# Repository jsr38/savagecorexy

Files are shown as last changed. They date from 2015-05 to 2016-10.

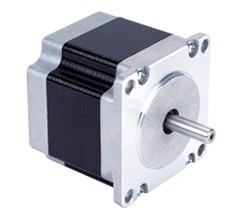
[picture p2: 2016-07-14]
datasheets/NEMA23-JKM-76mm_files/20131115143613461.jpg

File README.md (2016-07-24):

Savage CoreXY
=============

_NOTE_ This is still a work in progess, it is currently printing quite well.

This work was originally derived from [wolfmanjm/wolfhbot](https://github.com/wolfmanjm/wolfhbot) although since then it has diverged significantly and probably has very little in common now, although I retain the fork as provenance. 

A large build volume 3D printer based on the CoreXY concept.

It uses 4040 generic extrusions for most of the frame.

* The X carriage runs on Makerslide from [Amber Spyglass Ltd](http://amberspyglass.co.uk/)
* The Y carriages run on Makerslide from [Amber Spyglass Ltd](http://amberspyglass.co.uk/)
* The drive uses GT2 pulleys and belts
* the Belts have no cross over, they are stacked on top of each other instead
* build volume is large 300x1200x300 mm
* The Z platform has three stepper plus ballscrew Z actuators running on two 2040 Makerslides 
  with cast aluminium carriage. It runs on 1204 ballscrews.

Pictures and Videos
-------------------

* [first movements](https://youtu.be/KUbpFoaNcHg)
* [second movement](http://youtu.be/xxxxx)

Electronics and Firmware
------------------------

I used an Alligator Board with some modifications.  Details of the board are here:  [jsr38/AlligatorBoard](https://github.com/jsr38/AlligatorBoard)

My expansion board to allow alternative stepper drivers can be found here:  [jsr38/crocolulo](https://github.com/jsr38/crocolulo)

I'm currently running Repetier firmware on the Alligator.  My fork containing the current configuration is here: [jsr38/Alligator-Repetier-Firmware](https://github.com/jsr38/Alligator-Repetier-Firmware)

GT2 Belt Drive
--------------
The two end idlers are 2x flanged bearings back to back, and another pair separated with a washer above it,
Then two of the idlers on the X Gantry are raised to keep the belt riding level.
I avoid the cross over of the belts by running the two belts one above the other in parallel.

Z Bed
-----

The new Z actuator is a length of 500mm of 2040 VSlot, with a printed
carriage and v wheels. Driven by a McMaster ACME 1/2" leadscrew with
10TPI, Bearing blocks using 608 at top and bottom and a Nema17 with
5mm/0.25" flexible coupling. The bottom bearing block isolates the
flexible coupling from taking any weight and compressing. As the 1/2"
leadscrew is pretty big it has no wobble as far as I can tell and
having bearings top and bottom seems to be very stable. I also used a
printed Leadscrew nut printed in PLA and it seems pretty snug and
smooth. I also used a half height leadscrew nut and spring to implement
antibacklash which appears to be necessary.

There is a length of 2040 that spans from the Z actuator to the other
side of the frame where another 500mm length of 2040 VSlot has a vslot
mini carriage which is bolted to the end of the 2040 beam. Halfway
along this beam is a short piece of 2020 perpendicular to it, this
provides the third attachment point for the bed.

The most important part of this design is the
[moving knot](http://cockrum.net/cnc_mechanical.html), which is attached to
the top and bottom and runs over 4 v groove bearings on the cross
beam, This keeps the beam level while allowing a single actuator on one
end to move it up and down. This is the [far end](http://flic.kr/p/i67Sim),
and here is a view of the [whole assembly](http://flic.kr/p/i67Es7).

The bed is attached to the cross beam at three places to provide three
point bed levelling.  I use a scheme where a 4mm stud is screwed into
the tslots, and a 25mm length of aluminum rod, tapped to 4mm is
screwed onto that, this can be turned to move up and down the stud. At
the top of the aluminum is a cut out that the glass bed fits. Next to
this, and also bolted into the tslot, is an M4 bolt with a conical
spring bolted to the top, this pushes the glass at the three
attachment points up into the slots on the aluminum rounds. This keeps
the glass flat without deforming it, and allows it to be leveled at
three points by turning the aluminum rounds. Some jam nuts are used
to screw up to the aluminum rounds to stop them unscrewing once
levelled.

So this adds several printed parts... The Carriage, a bracket to hold
the leadscrew nut, and bearing blocks. Also some lathe work to cut a
thread into the center of some 1/2" aluminum round, and lathe a groove
at the top that the glass can slot into. (If the bed is not heated
this could be a printed part).

BOM
---
Aluminum parts are from Misumi with Misumi part numbers

* 10x 500mm HFS2020 20mm extrusions - frame
* 16x HBLFSN5 corner brackets - frame
* 2x  550mm HFS2020 - X Gantry sides
* 2x  85mm HFS2020 - X Gantry sides (Note it's cheaper to buy 2x 1000mm of 2020 and cut these yourself)
* 2x  540mm Makerslide - Y Rails
* 4x  HBLFSNF5 brackets - X Gantry
* 1x  500mm HFS2040 - Z Bed
* 1x  250mm HFS2020 - Z Bed
* 2x  Shapeoko motor mounts https://www.inventables.com/technologies/upgraded-shapeoko-motor-mount - Y carriages
* 12x VWheels https://www.inventables.com/technologies/dual-bearing-v-wheel-kit or http://openbuildspartstore.com/delrin-v-wheel-kit/
* lots of M5 nuts and bolts
* lots of M3 nuts and bolts
* 2x Nema 17 Stepper motors (preferably Kysan or equivalent)

Belt Drive
----------
* 10 meters GT2 belt
* 2 x GT2 pulleys 20 tooth
* 12 x 5mm flanged bearings for the idlers 

Printed Parts
-------------
* 1x motor-bracket-l.stl
* 1x motor-bracket-r.stl
* 1x x-carriage.stl

Z bed
-----
* 1x Nema 17
* 1x lead screw (McMaster 1/2" 10TPI ACME)
* Two printed Leadscrew nuts and a collar for the anti backlash
* 5/8" diameter spring for the anti backlash
* 2x 500mm 2040 VSlot
* 4x solid V Wheels http://openbuildspartstore.com/solid-v-wheel-kit/
* 1x printed Z carriage, plus leadnut holder
* 1x mini vslot carriage and mini wheels http://openbuildspartstore.com/mini-v-wheel-plate/
* 4x v groove bearings, 2x turnbuckles, two lengths of Spectra fishing line for the moving knot

Construction
------------

Getting the top of the frame square is essential, measure each end of the Y
rails to make sure they are parallel. Next the belts need to have exactly the
same tension to keep the X gantry straight, this was introducing non-square
prints for me. Loosen the X gantry on both Y carriages so it sits loosely on
the Y carriages, then measure the distance of each end of the X Gantry to the
front corner of the frame. Now tighten one or other belt until the X Gantry is
square to the Y rails, then tighten it down to the Y carriages.

If you find cylinders print out oblong or squares are not square this is
probably the problem.

License
-------

CC BY SA

<br /><span xmlns:dct="http://purl.org/dc/terms/" property="dct:title">WolfHBot</span> by <a xmlns:cc="http://creativecommons.org/ns#" href="http://wolfmanjm.github.com/wolfhbot" property="cc:attributionName" rel="cc:attributionURL">Jim Morris</a> is licensed under a <a rel="license" href="http://creativecommons.org/licenses/by-sa/3.0/deed.en_US">Creative Commons Attribution-ShareAlike 3.0 Unported License</a>.<br />Based on a work at <a xmlns:dct="http://purl.org/dc/terms/" href="https://github.com/wolfmanjm/wolfhbot" rel="dct:source">https://github.com/wolfmanjm/wolfhbot</a>.

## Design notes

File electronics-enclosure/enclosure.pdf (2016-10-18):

Made with Laser Cutter Ruby Gem (v1.0.3) Credits to Prawn for ruby PDF generation, and BoxMaker for inspiration.

Online: http://makeabox.io/
Source: https://github.com/kigster/laser-cutter units:
width:
height:
depth:
thickness:
notch:
kerf:
stroke:
padding:
margin:
page_size:

mm
250.0
250.0
50.0
3.0
30.0
0.06096
0.0254
2.54
3.175
custom

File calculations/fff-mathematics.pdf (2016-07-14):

# The Mathematics of Fused Filament Fabrication

### J. S. Reeve Independent Researcher

jsr [at] jsreeve.org

### July 14, 2016

## 1 Drive Mechanisms

### 1.1 Core XY

Equations of motion for a Core XY system are:

### 1.2 Delta

### 1.3 Drive Belts

For an endless belt, what is the circumference required to fit two pullies, radii r1, r2 and separation, d?

l = π (r1 + r2) + 2q
s

2 + (r2 − r1)

2
(1)

!!! This assumes r1 ≈ r2 !!! TODO

### 1.4 Steps per Unit Distance

Steps per millimeter of travel in the X direction:

1

## 2 Polymer Extrusion

### 2.1 Extruder Calibration

### 2.2 Volumetric Extrusion

## 3 Temperature

### 3.1 Thermistor Calibration

Thermistors, both NTC and PTC, and thermocouples are all used to sense temperatures at various critical locations on and around a typical FFF machine. See the Wikipedia page relating to thermistors: https://en.wikipedia.org/wiki/Thermistor. (https://en.wikipedia.org/wiki/Thermistor) A widely used third-order model developed for semiconductor resistance is the Steinhart-Hart equation.

1
T

= a + b ln(R) + c(ln(R))³ k(ln(R))² (2)

Coefficients a, b and c can be determined from empirically acquired data using a fitting method, in this case we choose least squares approximation. Starting from acquired data 1:
Summarising the least squares process and relating it to the numpy/scipy implementation referenced here: https://github.com/jsr38/savagecorexy/blob/cuboid/scripts/thermistor_calibration.py. (https://github.com/jsr38/savagecorexy/blob/cuboid/scripts/thermistor_calibration.py)
The general idea is to minimise the following norm:

kb − Axk

2

Suppose we took n measurements where:

x =

a
b
c
- , b =

1
T1

1
Tn

A =

1 | 1 | 1 | . . . | 1
ln(R1) | ln(R2) | ln(R3) . . . ln(Rn)
ln(R1)

3
| ln(R2)

3
| | ln(R3)

3
. . . ln(Rn)

3

This can be achieved by inversion of the matrix A. The following concerns the detail of generating a suitable lookup table given a circuit configuration and ADC of known resolution, that achieves the best resolution over our region of interest.

2

Resistance R | Temperature T
(k ohms) | (degrees celsius)
18.0 | 70.0
18.4 | 68.0
20.0 | 66.5
23.5 | 60.0
28.7 | 55.5
38.1 | 48.8
68.0 | 34.0
74.1 | 32.0
79.8 | 30.3
84.3 | 29.0
92.2 | 27.3
96.4 | 26.3
100.3 | 25.3
107.0 | 23.9
112.6 | 22.8
114.2 | 22.4
115.7 | 22.1
117.3 | 21.8
120.0 | 22.0
130.0 | 20.0

Table 1: Thermistor measurements peformed in lab.

The function used to generate lookup tables within the Repetier firmware assumes a different model, the β model which discounts the third order effects:

| 1
| T =

1
| T0

+

1
β

ln
R
R0
(3)

We could derive β and supply a pair of points to this function in order to generate a lookup table but since we have the third-order approximation we may as well use this to generate the lookup table. The accompanying script assumes a pull-up or pull-down resistor which linearises the thermistor response and hence reduces error introduced by finite resolution ADC, quantisation error, over our region of interest.

| N = 2B , B = 12, ∆b = 2B−L = 2⁴ = 16

3

n =

0 2¹ 2

2
. . . 2

L

αn =

n∆b +

∆b − 1
2

+

1
2

α =

α0 | α1 | α2 | . . . αn
=

Vo
Vi
Results of running the process on our data:

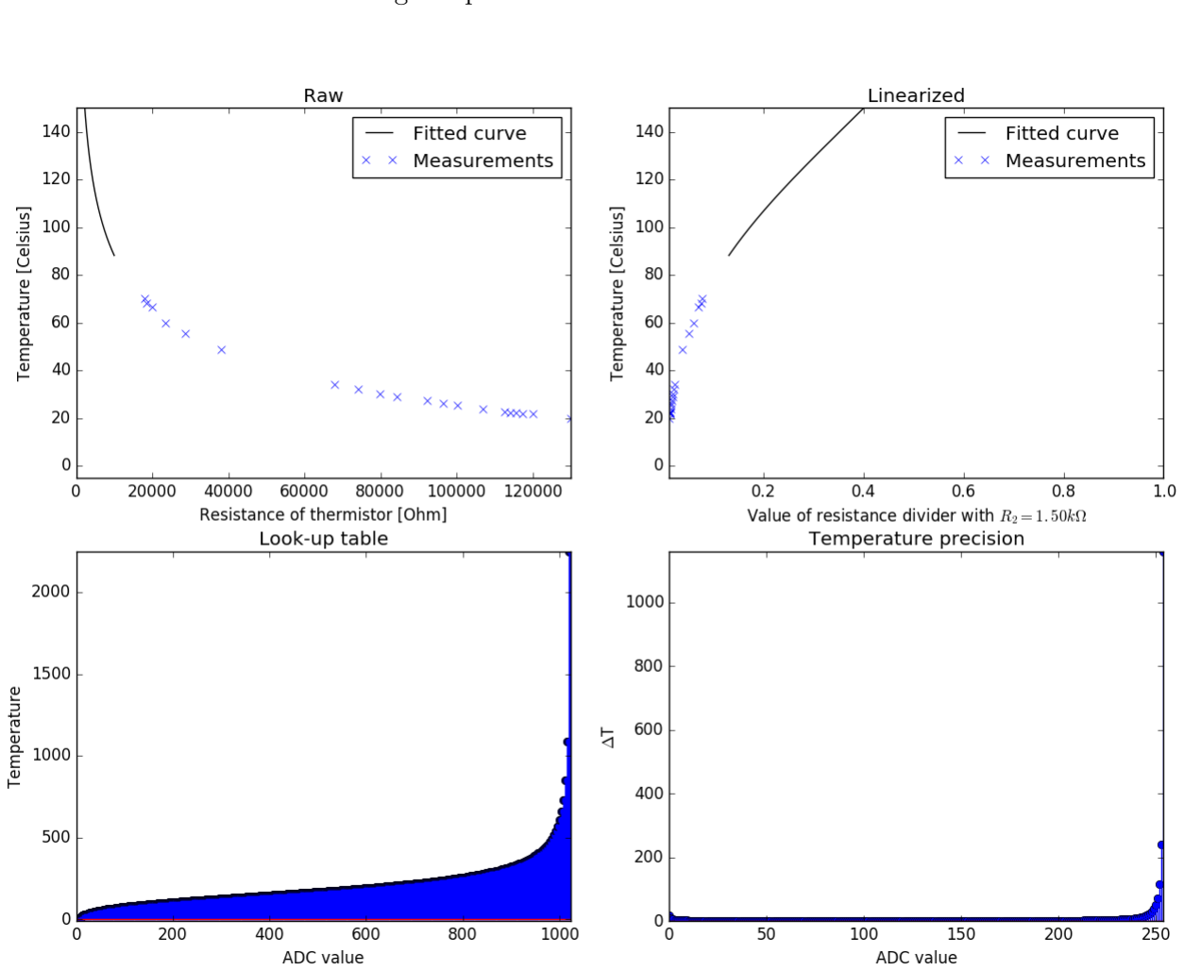
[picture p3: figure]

4

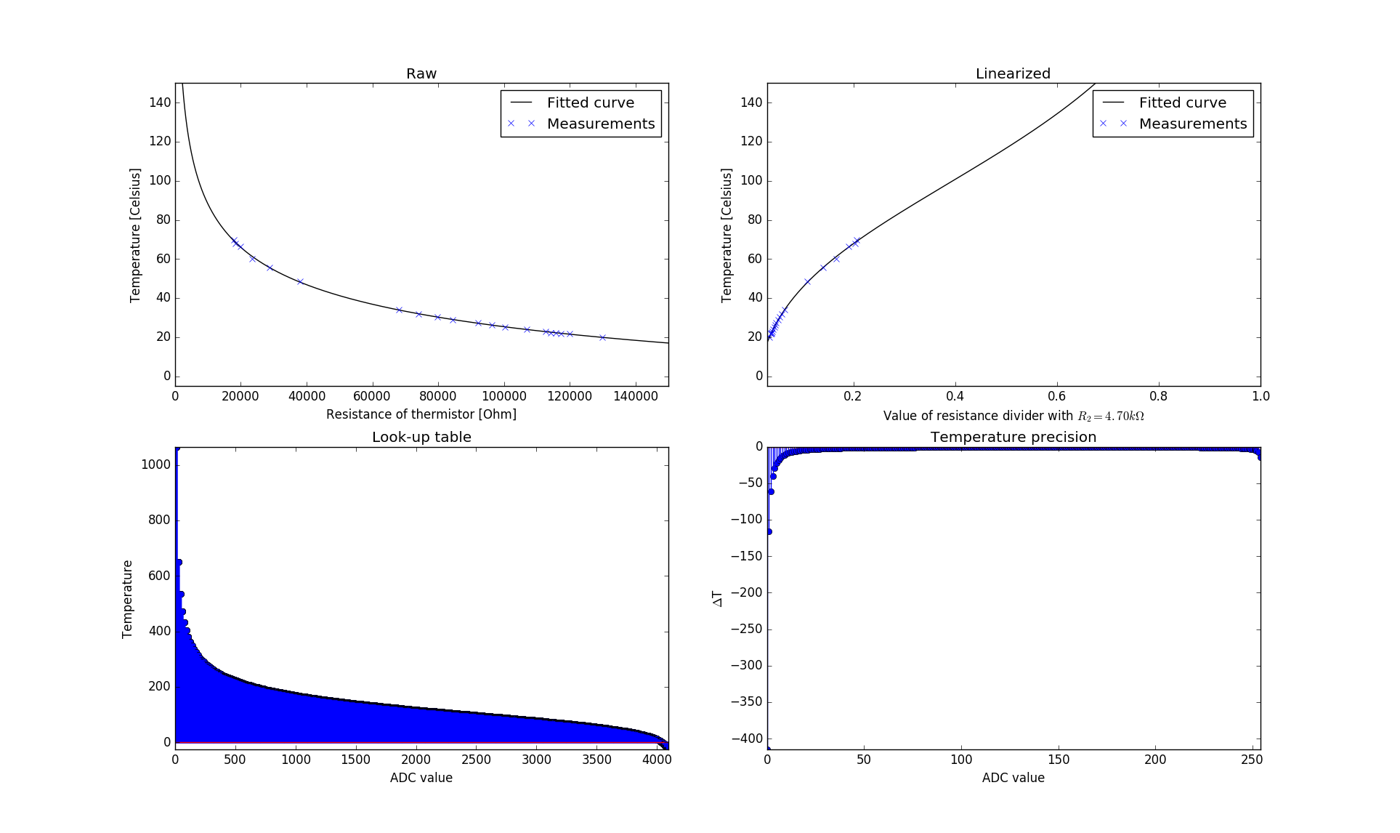
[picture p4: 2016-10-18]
scripts/thermistor_analysis.png

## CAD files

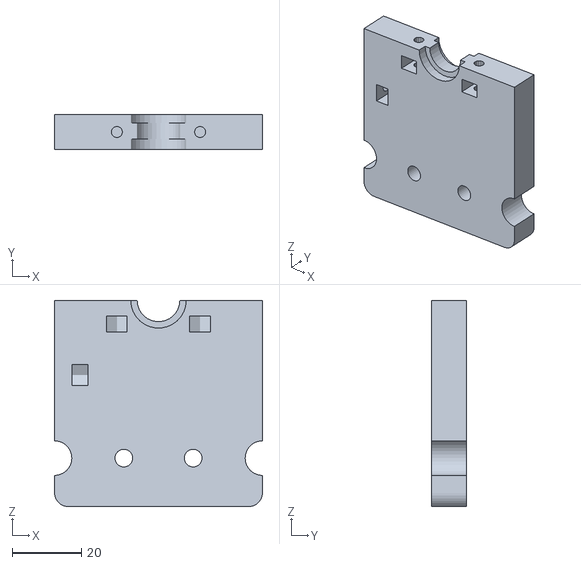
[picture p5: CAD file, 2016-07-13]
stl/E3D_clone_hot_end_mount_w_proximity_sensor_mountV2-main.stl
60.0 x 10.0 x 59.5

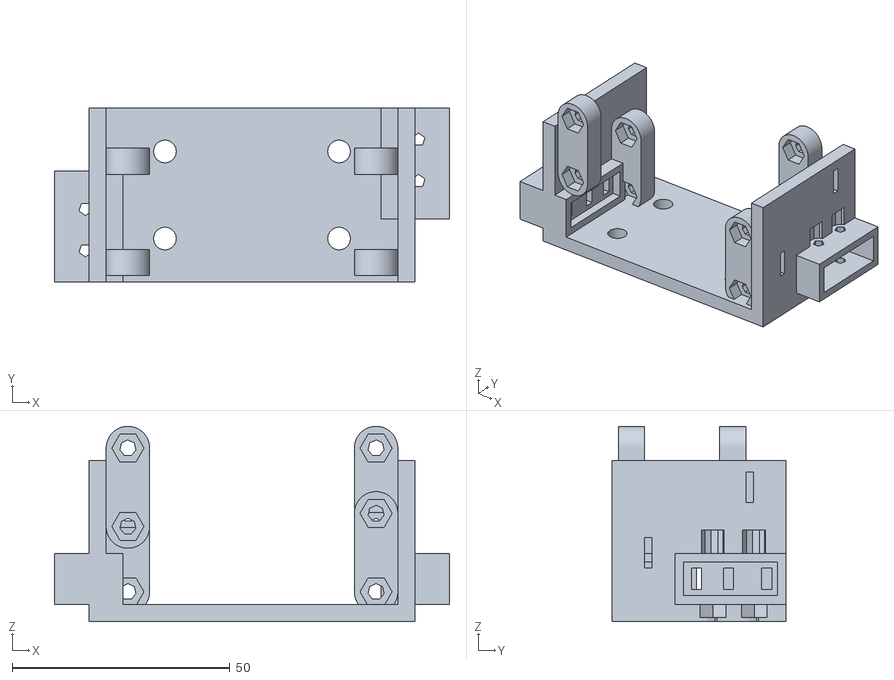
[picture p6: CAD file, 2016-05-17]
carriage-belt-clamp.stl
90.8 x 40.0 x 44.9

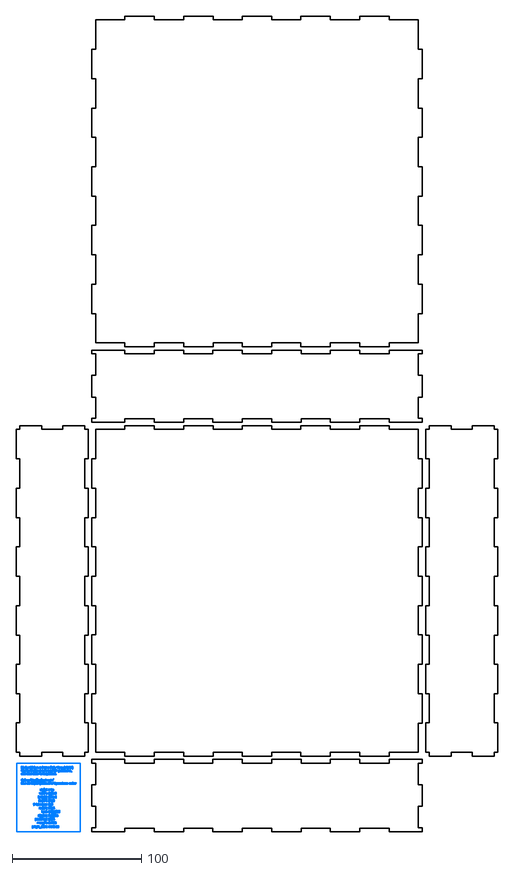
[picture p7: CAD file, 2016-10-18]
electronics-enclosure/enclosure.dxf
373.1 x 631.7

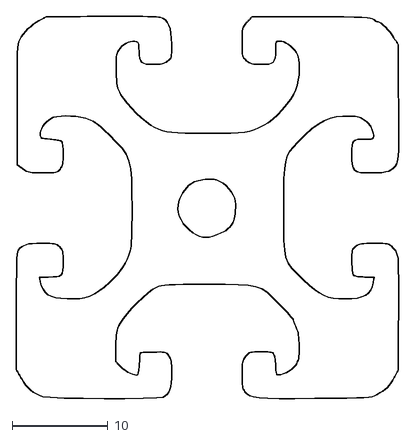
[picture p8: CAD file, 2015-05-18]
kjn/extrusion.dxf
40.0 x 40.0

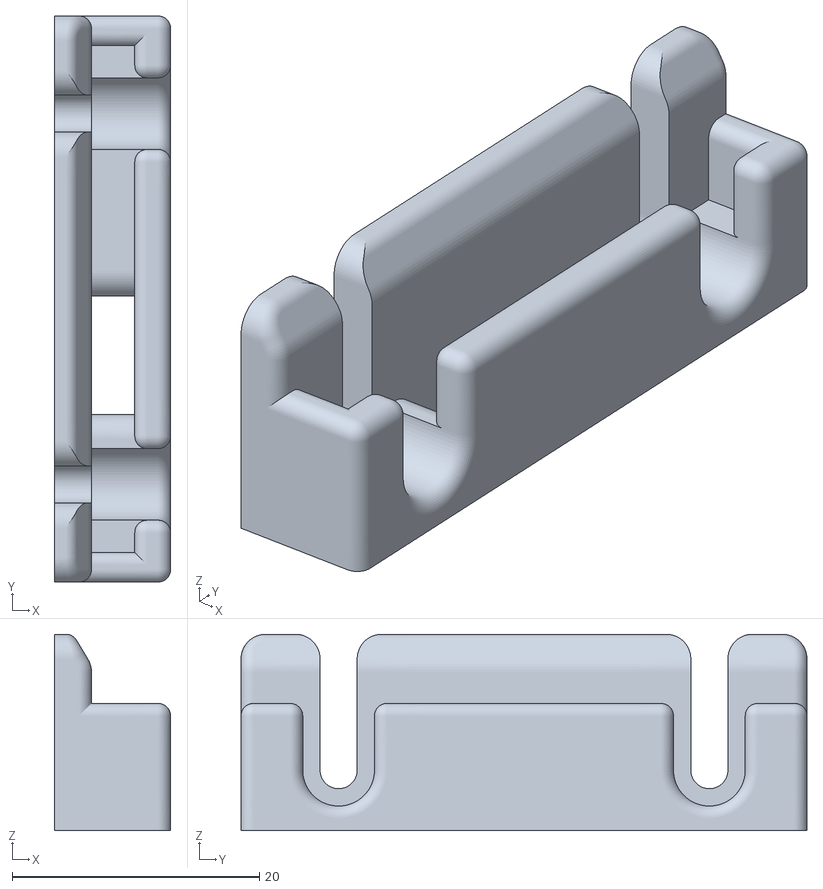
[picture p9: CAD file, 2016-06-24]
stl/fanduct/FanDuct-Bracket.stl
9.40 x 45.8 x 15.9

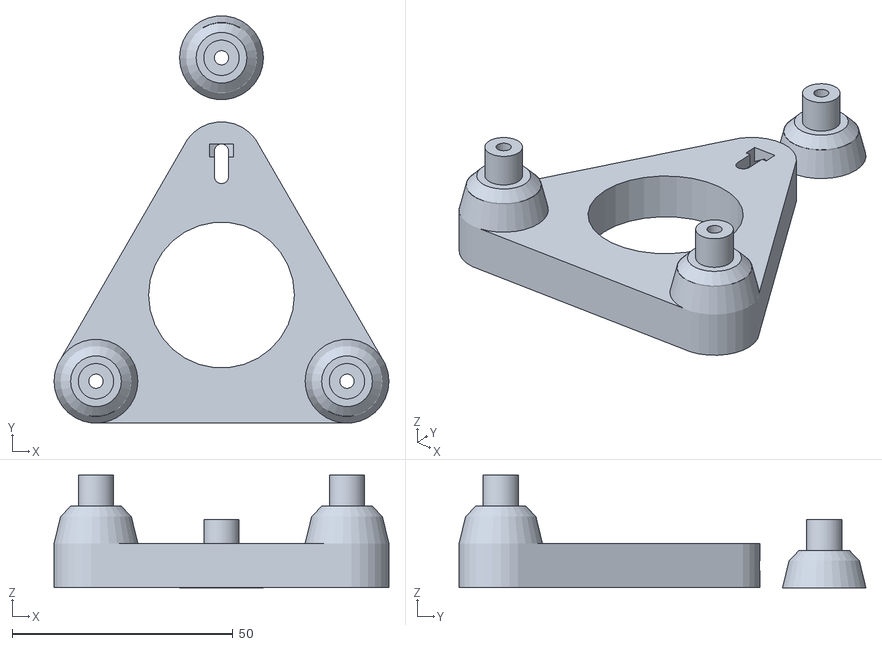
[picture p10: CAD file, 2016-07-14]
stl/y-carriage-src.stl
75.8 x 92.1 x 25.5

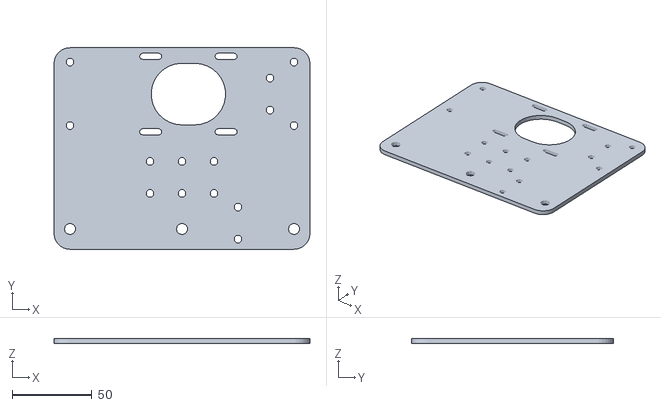
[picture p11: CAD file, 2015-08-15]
carriage_plate_motor_c14006_rev_1.stl
160.0 x 126.0 x 3.17

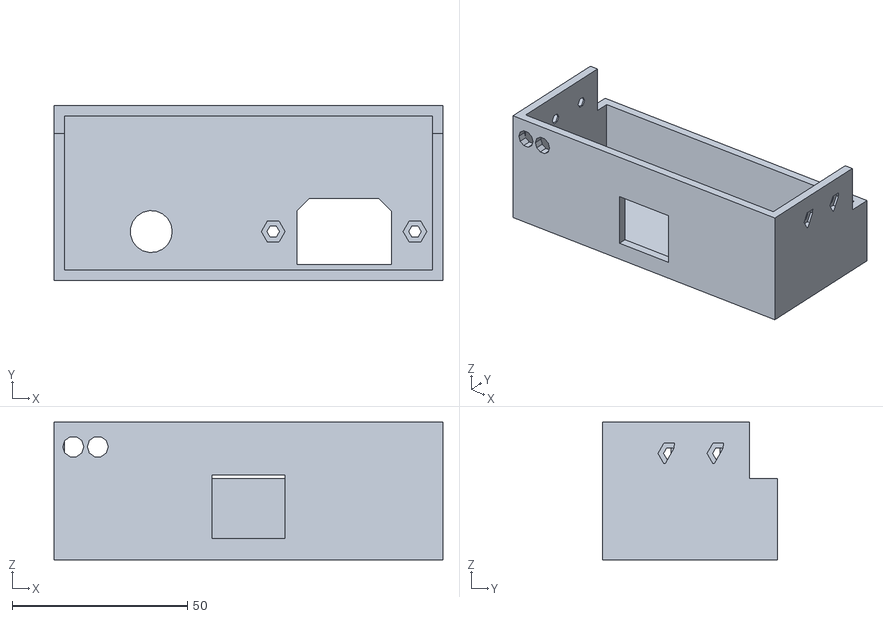
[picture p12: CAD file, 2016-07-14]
stl/power_supply_cover.stl
111.0 x 50.0 x 39.2

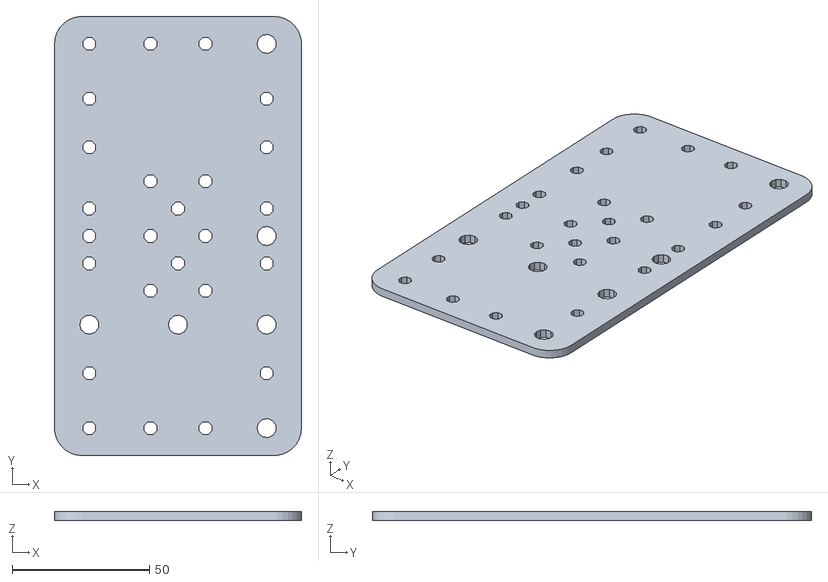
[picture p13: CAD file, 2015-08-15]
carriage_plate_standard_c14005_rev_2.stl
90.0 x 160.0 x 3.17

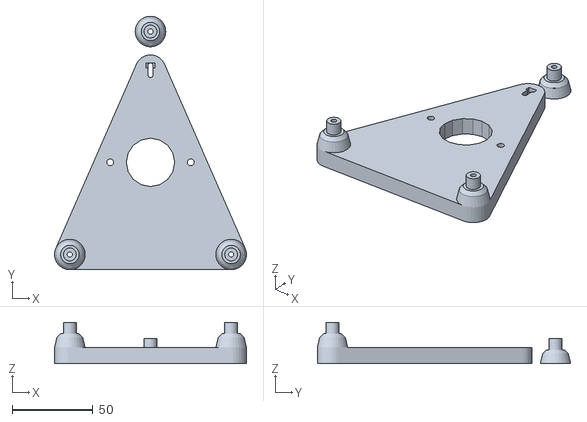
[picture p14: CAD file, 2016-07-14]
stl/x-carriage-src.stl
119.0 x 157.1 x 25.5

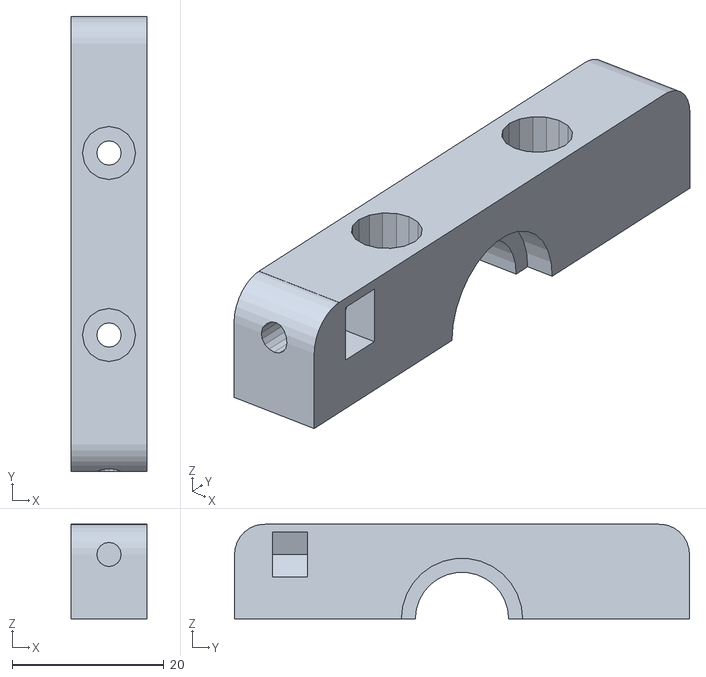
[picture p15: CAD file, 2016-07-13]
stl/E3D_clone_hot_end_mount_w_proximity_sensor_mountV2-clip.stl
10.0 x 60.0 x 12.5

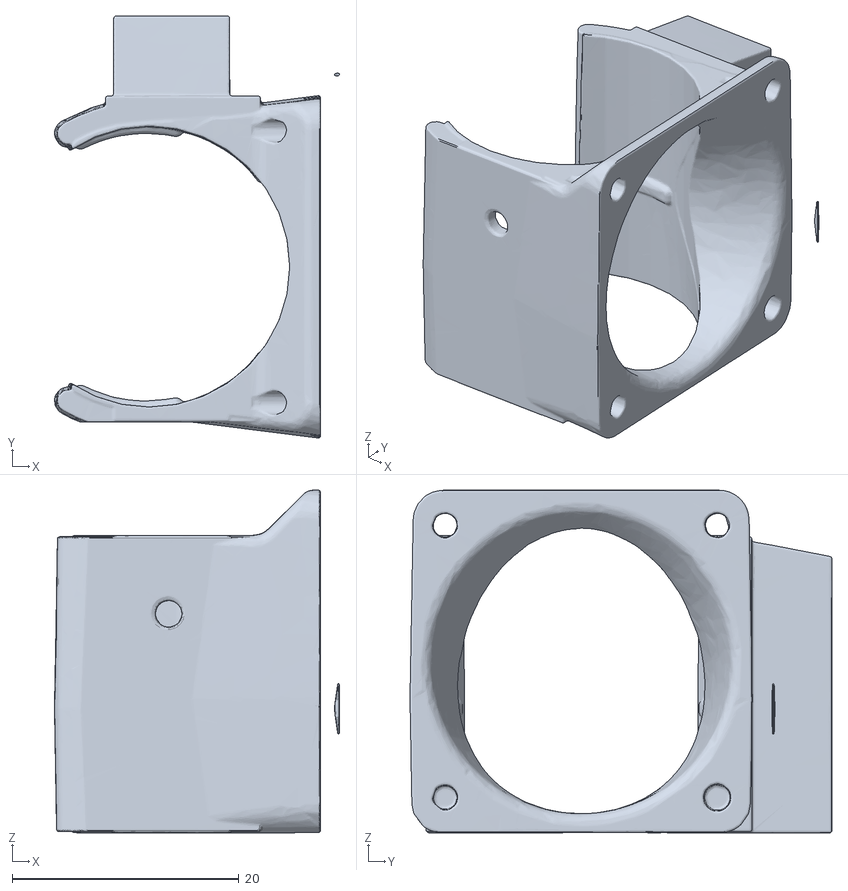
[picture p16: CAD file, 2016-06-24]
stl/E3DFANDUCT_.stl
25.2 x 37.2 x 30.2

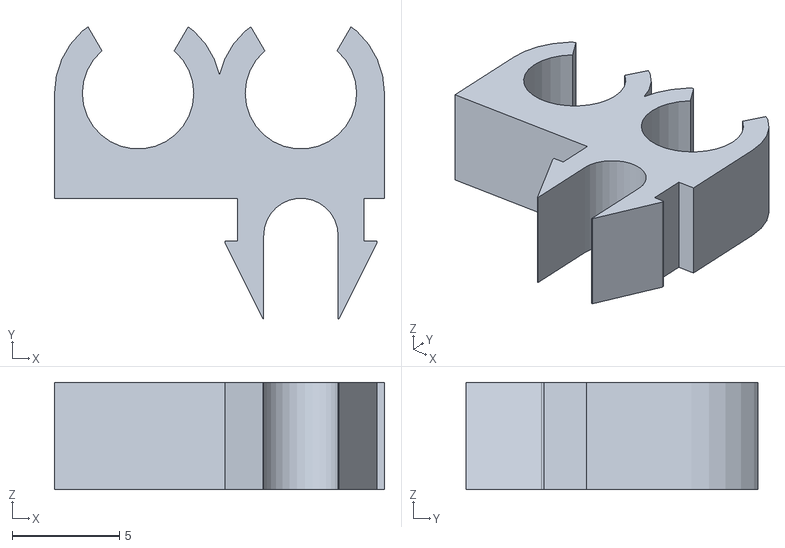
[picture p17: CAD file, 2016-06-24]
stl/Clip-060-double.stl
15.4 x 13.6 x 5.00

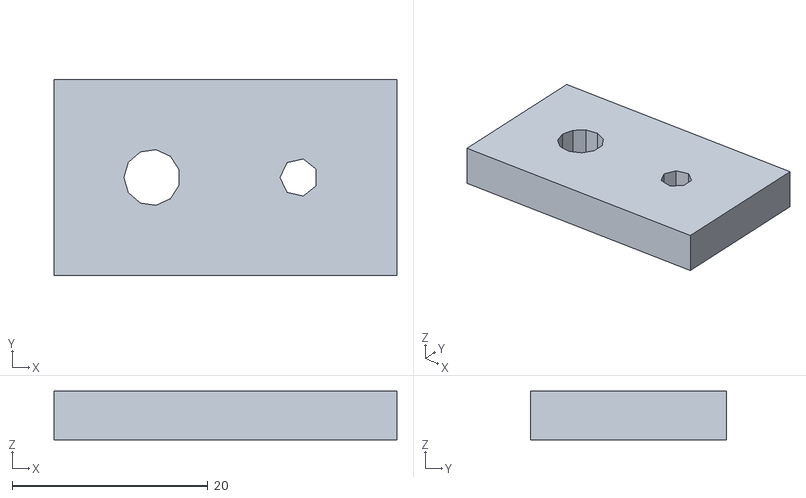
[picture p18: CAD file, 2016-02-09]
stl/electronics-mount-alligator.stl
35.0 x 20.0 x 5.00

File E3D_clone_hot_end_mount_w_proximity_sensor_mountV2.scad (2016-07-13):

//
//Mount for E3D hotend clone with mount for 18mm diameter proximity sensor
// this is designed to be bolted in place of the stock folgertech extruder,
// or any extruder mounted with holes the same width as Nema17 motor screws
//    this is part of the conversion to a bowden setup
// Designed by Lee Buell
// version1.0 December 30, 2015
// GPL v3.0
//  released under Creative Commons - Attribution - Share Alike licence (CC BY-SA)
//////////////////////////////////////////////////////////////////////////////////////
// it uses two libraries from the mendel90 design, available from here:
//
// https://github.com/T3P3/Mendel90/tree/LaserCut/scad
// teardrops.scad
// utils.scad
//
//
// this was designed for the E3D clone hot ends, by changing the JHeadDiameters below, it might work with a genuine E3D hot end
//  Explanation of JHeadDiameters numbers:
//    the first is the width of the narrow part of the mount (top)
//    the second is the  width of the wide part of the mount (top)
//    the third is the width of the bottom cooling fin area, I don't have a genuine E3D, but I believe this third number is the one to change



JHeadDiameters = [12.3, 16, 25];
JHeadDimensions = [4.05, 4.05+4.8, 12.3, 18.3, 50.1];

FanMountingHoleWidth=32; //32 for a 40mm fan
FlangeThickness=8;  // Thickness of mounting flange and Hot end mounting plate
HotendHeight=25;  // height of Hot End mount on mounting flange
FanWidth=40;
FanMountPitch = 30.0; // Mounting hole pitch for ducted fan
FlangeExtension=32.0;   //Length beyond fan with for hot end to mount
FlangeLength=FanWidth+FlangeExtension;// - 5.0;  //Total flange length
HotEndHeatSinkWidth=25; //width of heat sink, ?? for E3D  25 for chinese E3D clone
HotEndMountingThinArea=12.5;  //Thin band on the top of the HE
HotEndMountingWideArea=16.5;  //Wide bands on the top of the HE
HotEndMountingThinAreaHeight=5;  //Height of thin band
HotEndMountingWideAreaHeight=13;  //Height of wide band
ProxSensorDiameter=18.5;  //Diameter of proximity sensor
ProxSensorNutDiam=28.5;   //Diameter of proximity sensor nuts
ProxSensorLockWasherDiam=31;   //Diameter of proximity sensor LockWashers
ProxSensorDiameterMountFlangeWidth=ProxSensorNutDiam+7.5;
DistanceBetweenHE_Sensor=2;  //distand between the hot end and the proximity sensor
MountingHoleDistance=sqrt((FanMountingHoleWidth/2*FanMountingHoleWidth/2)*2);
CornerRadius=4;

CarriageMountHolePitch = 20;


print_clearance=0.1; //additional clearance between two printed objects

$fn=30;

rotate([-90,0,0])
translate([25,-FlangeThickness/2,30])
difference(){
CompleteHotEndMount();
translate([0,-(ProxSensorDiameterMountFlangeWidth+DistanceBetweenHE_Sensor+HotEndHeatSinkWidth/2+5)-50,0])
cube([100,100,100], center=true);
}
!difference(){
rotate([-90,0,90])
translate([25,(ProxSensorDiameterMountFlangeWidth+DistanceBetweenHE_Sensor+HotEndHeatSinkWidth/2+5),35])
CompleteHotEndMount();
translate([0,30,-50])
cube([120,100,100], center=true);
}


module CompleteHotEndMount(){
 difference(){
    union(){
      //Flange that mounts to x-carriage
      //mounting_flange();
	  
	   //Flange to mount Hot end
      translate([0,-FlangeExtension,-HotendHeight])
      rounded_rectangle([FanWidth + 20,FlangeLength,FlangeThickness+2],CornerRadius);

      }  //union
	  
      // Cavities
      // hole for proximity sensor
      //translate([0,-20,-40])
      //ProxSensorHole();
      
      
	  // hole for jhead mount
	  echo(ProxSensorDiameterMountFlangeWidth+DistanceBetweenHE_Sensor+HotEndHeatSinkWidth/2+5);
      translate([0,-(ProxSensorDiameterMountFlangeWidth+DistanceBetweenHE_Sensor+HotEndHeatSinkWidth/2+5),-HotendHeight-6])	  
      rotate([180,0,0])
      JHead(JHeadDiameters, JHeadDimensions);
	  
      // Mount holes for carriage
      translate([( - CarriageMountHolePitch) / 2.0,-10.0,-HotendHeight]) cylinder(r= 2.55, h = FlangeThickness + 4.0, center = true);
      translate([( CarriageMountHolePitch) / 2.0,-10.0,-HotendHeight]) cylinder(r= 2.55, h = FlangeThickness + 4.0, center = true);
      
	  
      // Cutout for V-wheel nuts on carriage
      translate([( - CarriageMountHolePitch * 3) / 2,-10.0,-HotendHeight]) cylinder(r= 5, h = FlangeThickness + 4.0, center = true);
      translate([( CarriageMountHolePitch * 3) / 2,-10.0,-HotendHeight]) cylinder(r= 5, h = FlangeThickness + 4.0, center = true);
      
      // holes for retainer cap	 
	  translate([12,-(FlangeLength+1),-25])
	  rotate([90,0,180])
	 Locknut_and_screwhole(Screwlength=16,DepthOfNut=22);
	 translate([-12,-(FlangeLength+1),-25])
	  rotate([90,0,180])
	  Locknut_and_screwhole(Screwlength=16,DepthOfNut=22);
	  
      // Holes for fan mount
      translate([-47,-FlangeLength + 8.0,-25]) rotate([90,0,90]) Locknut_and_screwhole(Screwlength=16,DepthOfNut=22);
      translate([-47,-FlangeLength + 8.0 + FanMountPitch,-25]) rotate([90,0,90]) Locknut_and_screwhole(Screwlength=16,DepthOfNut=22);
      
  } //difference
}  //module

module Locknut_and_screwhole(Screwlength=16,DepthOfNut=15){
//hole for m3 bolt followed by hex hole for m3 locknut
//hole for m3 bolt - with tight fit

nutheight=4.6;  // height of locknut as it sits flat on a table  // 4.5 when printed so nut is oriented flat, 4.5 was tight due to a stray hanging part of filament
LocknutDiamater=6.9;  //  Diameter of locknut with extra clearance added so it drops in but still grips the nut without slipping  //7.1 slipped - too large
screwheaddiamater=7;  //diamter of the head of the screw
ScrewheadHoleDiam=screwheaddiamater+.3; // remember the added value on the end witll be cut in half since since openscad uses radius measurements

LengthBeforeNut=DepthOfNut;
LengthAfterNut=3;

TotalNutLength=DepthOfNut+nutheight+LengthAfterNut;
RecessedHeadDepth=(TotalNutLength-1.5)-Screwlength;

//recessed hole for m3 screw
translate([0,0,-1])
cylinder(h=RecessedHeadDepth+1,r1=screwheaddiamater/2,r2=screwheaddiamater/2, center = false, $fn=16);

//hole for m3 screw
translate([0,0,0])
cylinder(h=TotalNutLength,r1=3/2+.1,r2=3/2+.1, center = false, $fn=16);

// hole for m3 locknut
translate([0,0,DepthOfNut])
rotate([0,0,30])    //rotate the flat sides of the hex nut
cylinder(h=nutheight,r1=LocknutDiamater/2,r2=LocknutDiamater/2, center = false, $fn=6);

//hole to drop nut into
translate([-LocknutDiamater/2+.475,-15,DepthOfNut])
rotate([0,0,0])   cube([(sqrt(3)*(LocknutDiamater/2)),15,nutheight]);
}  //module

module JHead(diameters = [12, 16, 25], dimensions = [3.7, 9.3, 12.3, 18.3, 50.1]) {
    color("Red") {
      // Top of JHead
      translate([0,0,-dimensions[0]])
        cylinder(d=diameters[1], h=dimensions[0]);
      translate([0,0,-dimensions[1]-0.01])
       cylinder(d=diameters[0], h=dimensions[1]-dimensions[0]+0.5);
      translate([0,0,-dimensions[2]])
        cylinder(d=diameters[1], h=dimensions[2]-dimensions[1]+.3);
      translate([0,0,-dimensions[3]])
        cylinder(d=9, h=dimensions[3]-dimensions[2]);
      translate([0,0,-dimensions[4]]) {
        // Radiator Volume
        cylinder(d=diameters[2], h=dimensions[4]-dimensions[3]);
        translate([0,0,-10]) {
          // Throat
          cylinder(d=6, h=10);
          // Heating Block
          translate([0,5,0])
            cube([20,20,10], center=true);
          // Nozzle
          translate([0,0,-12])
            cylinder(d1=1, d2=5, h=3);
          translate([0,0,-9])
            cylinder(d=10, h=5, $fn=6);
        }
      }
    }
  }

module HotEndMountHole(){
      //thin par of Hot end neck
     cylinder(h=20, r=HotEndMountingThinArea/2, $fn=20);
     // top wide part of Hot end neck
     translate([0,0,-15])
     cylinder(h=20, r=HotEndMountingWideArea/2, $fn=20);
     // bottom wide part of Hot end neck
     translate([0,0,10])
     cylinder(h=10, r=HotEndMountingWideArea/2, $fn=20);

}  // module

module ProxSensorHole(){
  //round hole for sensor
  cylinder(h=80, r=ProxSensorDiameter/2, $fn=20);
  //hex hole for nut
  translate([0,0,-2]) rotate([0,0,30])
  cylinder(h=40, r=ProxSensorNutDiam/2, $fn=6);
}  // module
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

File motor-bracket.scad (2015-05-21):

use <misumi-parts-library.scad>;
use <MCAD/stepper.scad>
use <MCAD/motors.scad>
use <MCAD/triangles.scad>
use <motor-mount.scad>
use <myLibs.scad>

thick= 5.6;
w= 54;
h= 55;

%translate([-20,20,0]) corner();
motor_bracket(1);

module motor_bracket(r=0) {
	mirror([0,r,0]) difference() { 
		union() {
			rotate([0,0,90]) corner_bracket();
			translate([thick,50/2+10,0]) rotate([0,0,-90])  motorPlate(thick, thick);
		}
		// mounting holes
		#translate([-1,10,h+3]) rotate([0,90,0]) hole(5, thick+2);
		translate([-1,20+25,20]) rotate([0,90,0]) slot(d=5, l=30,ht=thick+2);
		translate([-10,-thick-1,h]) rotate([0,90,90]) hole(5, thick+2);
		translate([-10,-thick-1,h-h/3]) rotate([0,90,90]) hole(5, thick+2);
		translate([-10,-thick-1,h/4]) rotate([0,90,90]) hole(5, thick+2);	}

}

module motorAttachment(thickness=4) {
        translate([0,h,thickness]) rotate([180,0,0]) difference() {
                cube([w,h,thickness]);
                translate([w/2,h/2,-1]) linear_extrude(height=thickness+2) stepper_motor_mount(17,8,true,0.1);
        }
}

module attachmentPlate(thickness=4) {
	cube([w,40,thickness]);
}

module buttress(thickness=4) {
        triangle(50, 40, thickness);
}

module motorPlate(thickness=4, buttressThickness=4) {
        union() {
                motorAttachment(thickness);
                translate([0,0.1,0]) rotate([90,0,0]) attachmentPlate(thickness);
                translate([buttressThickness,-0.1,0]) rotate([0,-90,0]) buttress(buttressThickness);
                translate([w,-0.1,0]) rotate([0,-90,0]) buttress(buttressThickness);
        }
}


module corner() {
	translate([10,0,10]) hfs2020(80);
	translate([0,-10,10]) rotate([0,0,90]) hfs2020(80);
	translate([10,-10,0]) rotate([90,0,0]) hfs2020(80);
}

module corner_bracket() {
	translate([-thick,-thick,0]) union() {
		cube([20+thick,thick,h+20-thick]);
		cube([thick,20+thick,h+20-thick]);
		translate([20,0,0]) cube([40,thick,40]);
	}
}

//module smount(w=50,l=50) {
//	translate([0,0,thick/2]) difference() {
//		cube([w,l,thick], center=true); 
//		translate([0,0,-thick/2-1]) linear_extrude(height= thick+2) stepper_motor_mount(nema_standard=17,slide_distance=5, mochup=false, tolerance=0.1);
//	}
//}

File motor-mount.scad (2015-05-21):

use <MCAD/motors.scad>
use <myLibs.scad>
use <MCAD/triangles.scad>

w= 54;
h= 50;

function motorMountWidth() = w;
function motorMountHeight() = h;

module motorAttachment(thickness=4) {
	translate([0,h,thickness]) rotate([180,0,0]) difference() {
		cube([w,h,thickness]);
		translate([w/2,h/2,0]) linear_extrude(height=thickness+1) stepper_motor_mount(17,5,true,0.1);
	}
}

module attachmentPlate(thickness=4) {
	difference() {
		cube([w,40,thickness]);

		// attachment holes
		#translate([(w/2)-10, 10, 0]) rotate([0,0,90]) slot(d= 5, l=10, ht=thickness);
		#translate([(w/2)-10, 30, 0]) rotate([0,0,90]) slot(d= 5, l=10, ht=thickness);
		#translate([(w/2)+10, 10, 0]) rotate([0,0,90]) slot(d= 5, l=10, ht=thickness);
		#translate([(w/2)+10, 30, 0]) rotate([0,0,90]) slot(d= 5, l=10, ht=thickness);
	}
}

module buttress(thickness=4) {
	triangle(50, 40, thickness);
}

module motorPlate(thickness=4, buttressThickness=4) {
	translate([-w/2, thickness, 0]) union() {
		motorAttachment(thickness);
		translate([0,0.1,0]) rotate([90,0,0]) attachmentPlate(thickness);
		translate([buttressThickness,-0.1,0]) rotate([0,-90,0]) buttress(buttressThickness);
		translate([w,-0.1,0]) rotate([0,-90,0]) buttress(buttressThickness);
	}
}

motorPlate(5, 5);
//motorAttachment();
//attachmentPlate();
//buttress();

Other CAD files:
stl/PCB_ALLIGATOR.STL
stl/shim_10mm.stl
stl/nema23-z-mount.stl
stl/drill-guide-z.stl
Clip-060.scad
Pulley_T-MXL-XL-HTD-GT2_N-tooth.scad
ballscrew_lower.scad
ballscrew_upper.scad
ballscrew_z_mount.scad
ballscrew_z_mount_centre.scad
bedleveller.scad
belt-clamp_GT2.scad
bracket4040.scad
carriage-belt-clamp.scad
drill-guide-z.scad
drill-guide.scad
drill_guide_makerslide.scad
dxf/b17022_rev_2.dxf
electronics-enclosure/enclosure.scad
electronics-mount-alligator.scad
foot.scad
hbot-frame.scad
hex-nut.scad
idler-gantry-v2.scad
idler-plate.scad
idler-v2.scad
kjn-parts-library.scad
microswitch-cutout.scad
nema23-z-mount.scad
power_supply_cover.scad
rounded-box.scad
shim_10mm.scad
src/motor-mount.scad
src/sprocket_with_tolerance.scad
stl/ballscrew_lower.stl
stl/ballscrew_upper.stl
stl/ballscrew_z_mount.stl
stl/ballscrew_z_mount_centre.stl
stl/drill-guide.stl
stl/drill_guide_makerslide.stl
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

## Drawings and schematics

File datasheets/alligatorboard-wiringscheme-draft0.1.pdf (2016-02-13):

Alligator Board – Wiring Diagram | draft 0.1

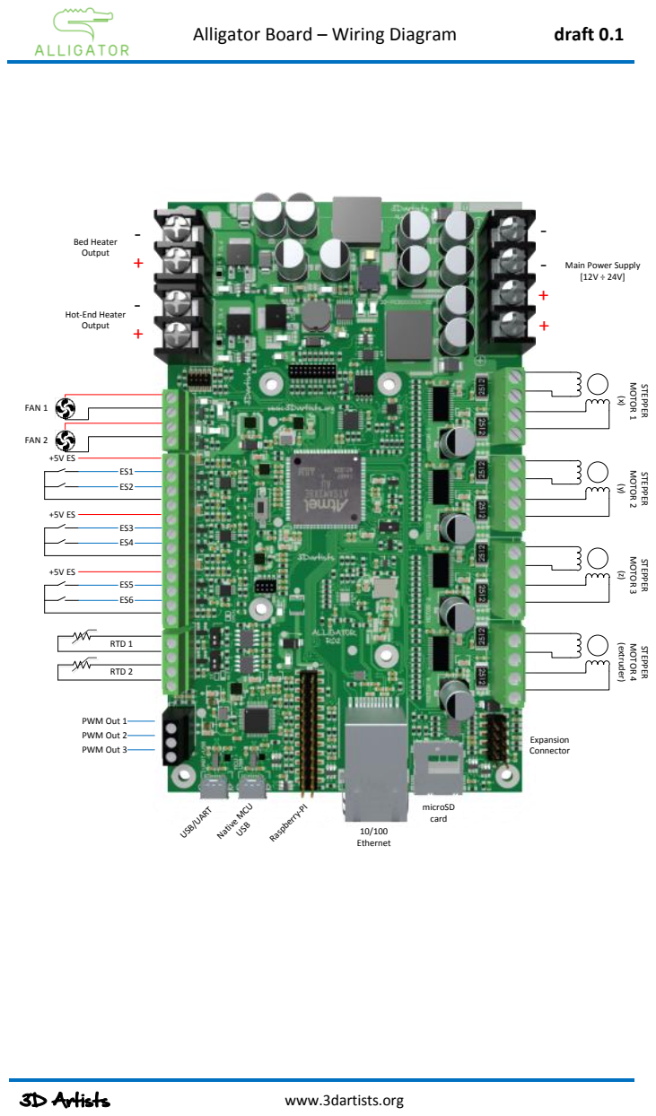
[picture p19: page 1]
3D Artists; www.3dartists.org; FAN 1; FAN 2; RTD 1; RTD 2; USB/UART; Raspberry-PI; 10/100 Ethernet; microSD card; Expansion Connector

STEPPER MOTOR 1 (x) STEPPER MOTOR 2 (y) STEPPER MOTOR 3 (z) STEPPER MOTOR 4 (extruder) Main Power Supply [12V ÷ 24V] -

Bed Heater Output

Hot-End Heater Output

PWM Out 1 PWM Out 2 PWM Out 3

Native MCU USB

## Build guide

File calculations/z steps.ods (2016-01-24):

mm/rotation | steps/rotation | microsteps | length | h | d | minh | maxd
2.54 | 3200 | 16 | 165 | 200 | 10 | 72.9451848993 | 148
layer ht | steps/mm | mm/step | tiers |  |  | min | max
0.3 | 1259.842519685 | 0.000793750 | 1 |  | max error between | 65 | 320 | mm | 216 | $H$216
 |  | 0.012700000 |  |  | 0.00444 |  |  |  | 1066 | $H$1066
 |  |  |  | max d | 299.48295 | travel |  |  |  |  |  | max error
 |  |  |  | min d | 0.00007 | 299.4828876009 |  |  |  |  |  | 0.00039375
 |  | 165
layer ht | h | d | Absolute steps | actual step | actual d | actual h | error in ht mm |  | steps | actual steps | actual move | error
0.3 | 0.15 | 164.9999318182 | 0.0858983714 | 0 | 165 | 0 | 0.15 |  | 377.9527559055 | 378 | 0.3000375 | 0.0000375
0.6 | 0.3 | 164.9997272725 | 0.3435936984 | 0 | 165 | 0 | 0.3 |  | 755.905511811 | 756 | 0.600075 | 0.000075 | 0.000075
0.9 | 0.45 | 164.9993863625 | 0.7730866201 | 1 | 164.99920625 | 0.5117976846 | 0.0617976846 |  | 1133.8582677165 | 1134 | 0.9001125 | 0.0001125 | 0.0001125
1.2 | 0.6 | 164.9989090873 | 1.3743782012 | 1 | 164.99920625 | 0.5117976846 | 0.0882023154 |  | 1511.8110236221 | 1512 | 1.20015 | 0.00015 | 0.00015
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

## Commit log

2015-05-19 Make frame a cuboid rather than a cube. WIP
    [hbot-frame.scad]
2015-05-21 correct path for MCAD imports and add 4040 bracket first pass
    [bedleveller.scad, bracket4040.scad, leadscrew-bearing-block.scad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]
2015-05-24 y-carriage extrusion width to 40mm
    [y-carriage.scad]
2015-05-24 Add a foot for the upright frame extrusions
    [foot.scad, rounded-box.scad]
2015-05-25 Improve foot by removing central pillar. Otherwise it'd be a tighter fit as we scale the extrusion up to give some extra tolerance.
    [foot.scad, foot.stl]
2015-05-25 Add metric-cerberus as submodule as we depend on mushroom() and extrusion4040_no_hole(), well, eventually we will.
2015-05-25 Use extrusion that scales each surface of the shape in the direction of the normal of the interface between plastic and air - more room
    [foot.scad, foot.stl]
2015-05-31 Add a drilling guide for drilling the aluminium profile extrusion.
    [drill-guide.scad, drill-guide.stl]
2015-06-03 Improve drill guide and fix a few bugs.
    [drill-guide.scad, drill-guide.stl, foot.scad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]
2015-06-04 Make the drill guide holes larger, now 2mm diameter. Add 1mm to the radius of the previously 4mm radius support structures for the guide holes.
    [drill-guide.scad, drill-guide.stl]
2015-06-12 Add pulley source and modify drill guide to correct scale factor bug and reduce dril holes to 1.75mm diameter
    [Pulley_T-MXL-XL-HTD-GT2_N-tooth.scad, drill-guide.scad, drill-guide.stl]
2015-06-13 Add a motor mount for NEMA23 stepper motor.
    [nema23-mount.scad, nema23-mount.stl]
2015-07-31 Update xy motor mount to have mounting holes along the horizontal extrusion rather than the vertical where the Makerslide rails are screwed in
    [nema23-mount.scad]
2015-08-15 Add idler-gantry-v2 and add switch to generate either left or right xy motor mount
    [carriage_plate_motor_c14006_rev_1.stl, carriage_plate_standard_c14005_rev_2.stl, idler-gantry-v2.scad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]
2015-08-15 Countersink mount screws
    [idler-gantry-v2.scad]
2015-08-15 Correct height for gantry idler
    [idler-gantry-v2.scad]
2015-08-16 Create idler model (non-carriage version). Refactor idler into idler top and bottom plate. Modify motor mounts to sit at correct height with gap to allow belt to pass through. Add Jospeh Prusa's GT2 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
    [belt-clamp_GT2.scad, carriage-belt-clamp.scad, idler-gantry-v2.scad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]
2015-08-22 +5mm offset for motor boss
    [nema23-mount.scad]
2015-10-25 Add drill guides to drill the z axis frame parts.
    [drill-guide-z.scad, drill-guide-z.stl, drill_guide_makerslide.scad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]
2015-11-17 Add ballscrew upper support
    [ballscrew_upper.scad]
2015-12-13 Modify ballscrew_upper to suit Makerslide
    [b17022_rev_2.dxf, ballscrew_lower.scad, idler-gantry-v2.scad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]
2015-12-27 Develop ballscrew_z_mount and add pdf of Makerslide profile
    [ballscrew_z_mount.scad]
2016-01-02 Tweak tolerances. Ahem... Include them where they should have been.
    [ballscrew_z_mount.scad]
2016-01-03 Add centre z ballscrew mount. TODO: cut the extrusion profile a bit longer instead of this nonsense :)
    [ballscrew_z_mount_centre.scad]
2016-01-03 Add shim
    [shim_10mm.scad]
2016-01-21 Add z stepper mounts.
    [nema23-z-mount.scad]
2016-01-21 Make modifications to z stage nema23 mount and add various latest stl files.
    [ballscrew_lower.stl, ballscrew_upper.stl, ballscrew_z_mount.stl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]
2016-01-23 Initial commit of belt calculations.
2016-01-24 Move step calculation spreadsheet to calculations dir and remove leadscrew* files
    [leadscrew-bearing-block.scad, leadscrewnut_0.5in-10tpi.scad, leadscrewnut_0.5in.scad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]
2016-01-24 First stab at microswitch end-stops
    [ballscrew_upper.scad]
2016-01-24 More microswitch recess work
    [ballscrew_upper.scad]
2016-01-29 Add Alligator protector and latest end-stop modifications to ballscrew_upper
    [PCB_ALLIGATOR.STL, ballscrew_upper.scad]
2016-01-29 More end-stop improvements WIP
    [ballscrew_upper.scad]
2016-01-29 Rough end-stop WIP
    [ballscrew_upper.scad]
2016-02-09 Update ballscrew upper mount to incorporate microswitch endstops
    [ballscrew_upper.scad, ballscrew_upper.stl]
2016-02-09 Add electronics mount.
    [electronics-mount-alligator.scad, electronics-mount-alligator.stl]
2016-02-10 Fix bug and loosen up tolerances a bit.
    [ballscrew_upper.scad, ballscrew_upper.stl]
2016-02-10 Conditional end-stops
    [ballscrew_upper.scad]
2016-02-10 Latest STL
    [ballscrew_upper.stl]
2016-02-19 Add stepper driver and Cortex-M debug connector data sheets
2016-05-17 Modify carriage to add microswitch end stops and recesses for captive belt clamp nuts.
    [carriage-belt-clamp.scad, carriage-belt-clamp.stl, hex-nut.scad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]
2016-06-24 Add Makerslide cable clips, fan duct, hot end mount and associated STLs
    [Clip-060-double.stl, Clip-060.scad, E3DFANDUCT_.stl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]
2016-07-13 Update hot end mount to include fan duct clip. Add datasheets for 12V PSU (unused as LT2596 buck convertor employed). Add thermistor calibration script and measured data for E3D clone.
    [E3D_clone_hot_end_mount_w_proximity_sensor_mountV2-clip.stl, E3D_clone_hot_end_mount_w_proximity_sensor_mountV2-main.stl, E3D_clone_hot_end_mount_w_proximity_s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]
2016-07-14 Add break-in code. Make a start on thermistor calibration documentation. Add NEMA23 datasheet. Rename calculations document belt-system -> fff-mathematics
    [idler-v2.scad, power_supply_cover.scad, power_supply_cover.stl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]
2016-07-14 Add a pull up/down circuit configuration option. Follow Google Style Guide on constants (capitalise)
2016-10-15 Add laser cut electronics enclosure. **WIP**
    [enclosure.dxf, enclosure.scad]
2016-10-18 Update electronics enclosure. Update thermistor calibration script.
    [enclosure.dxf, enclosure.scad]
